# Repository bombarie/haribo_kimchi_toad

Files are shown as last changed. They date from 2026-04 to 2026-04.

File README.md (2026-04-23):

# Jaha Koo - Toad

Code and PCB design for the transmitter and receiver + driver board to control the Toad robot. The wireless control is achieved ising an ExpressLRS wireless link, controlled and read using arduino-compatible microcontrollers. The Toad uses Dynamixel smart servo motors. The host board in the Toad contains a Dynamixel motor driver board, an open-source board designed by [Josue Alejandro Gutierrez](https://github.com/JosueAGtz/dynamixelInterface) and fabbed by me.

Produced for [Campo](https://campo.nu).

## Current files
* Code
  * Toad control from desktop (Chataigne) - [toad_v07_increment_CCs](./chataigne/toad_v07_increment_CCs.noisette)
  * Midi-host transmitter code
    * transmitter #1 (Wemos S2 mini) - [CRServoF_lib_tx_v02_add_midi.cpp](/arduino/platformio/WEMOS_ESP32S2_MIDI_ELRSTX/src/CRServoF_lib_tx_v02_add_midi.cpp)
    * transmitter #2  (Wemos S3 mini) - [CRServoF_lib_tx_v02_add_midi.cpp](./arduino/platformio/wemos_s3_mini/src/CRServoF_lib_tx_v02_add_midi.cpp)
  * Toad receiver code (Xiao esp32-c3): [toad_dynamixel_examples_moveServo_v08_update_to_arduino_core_3.cpp](./arduino/platformio/esp32c3_helloworld/esp32c3_helloworld/src/toad_dynamixel_examples_moveServo_v08_update_to_arduino_core_3.cpp)
* PCB - [toad_mainboard_v03](./kicad/toad%20mainboard%20v01/toad_mainboard_v03/toad_mainboard_v03.kicad_pro)

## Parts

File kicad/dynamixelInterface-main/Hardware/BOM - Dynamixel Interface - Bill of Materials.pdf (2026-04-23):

# BOM - Dynamixel Interface

# | Reference | Part Number | Description | Manufacturer | Distribuitor | Quantity

1 | U1 | TXB0104PWR | Translation - Voltage Levels 4-Bit Bi-directional V-Level Translator | TI | MOUSER | 1
2 | U2 | SN74LVC2G241DCTR | Buffers & Line Drivers Tri-State Dual | TI | MOUSER | 1
3 | R1, R2, R3, R4 | ERJ-2RKF1001X | Thick Film Resistors - SMD 0402 1KOhm 1% AEC-Q200 | PANASONIC | MOUSER | 4
4 | R5 | ERJ-2RKF1002X | Thick Film Resistors - SMD 0402 10KOhms 1% AEC-Q200 | PANASONIC | MOUSER | 1
5 | C1 | 885012105012 | Multilayer Ceramic Capacitors MLCC - SMD/SMT WCAP-CSGP 1uF 0402 20% 10V MLCC | WE | MOUSER | 1
6 | C2, C5 | 885012205037 | Multilayer Ceramic Capacitors MLCC - SMD/SMT WCAP-CSGP 0.1uF 0402 10% 16V MLCC | WE | MOUSER | 2
7 | C3 | 885012206076 | Multilayer Ceramic Capacitors MLCC - SMD/SMT WCAP-CSGP 1uF 0603 10% 25V MLCC | WE | MOUSER | 1
8 | C4 | 885012106031 | Multilayer Ceramic Capacitors MLCC - SMD/SMT WCAP-CSGP 10uF 25Vol 20% | WE | MOUSER | 1
9 | D1, D2 | APHHS1005SECK | Standard LEDs - SMD ORANGE WTR CLEAR 160mcd 610nm | KINGBRIGHT | MOUSER | 2
10 | D3 | APHHS1005QBC/D | Standard LEDs - SMD Blue 470nm Water Clear | KINGBRIGHT | MOUSER | 1
11 | D4 | APHHS1005CGCK | Standard LEDs - SMD GREEN WTR CLEAR 40mcd 574nm | KINGBRIGHT | MOUSER | 1

Optional

12 | J1 | 22-05-7035 | Headers & Wire Housings 3 CKT 2.5MM R/A HDR | MOLEX | MOUSER | 1
13 | J1 | S3B-EH(LF)(SN) | CONN HEADER R/A 3POS 2.5MM | JST | DIGIKEY | 1

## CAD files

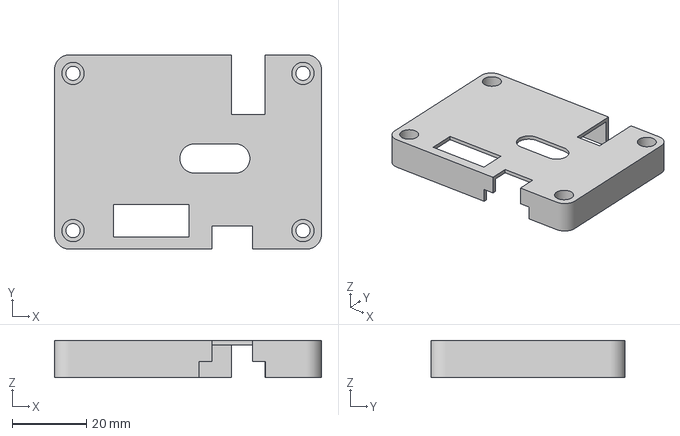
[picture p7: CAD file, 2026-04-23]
3mf/Jaha Koo - Toad - pcb housing v1 - bottom.3mf
72.0 x 52.4 x 10.0 mm

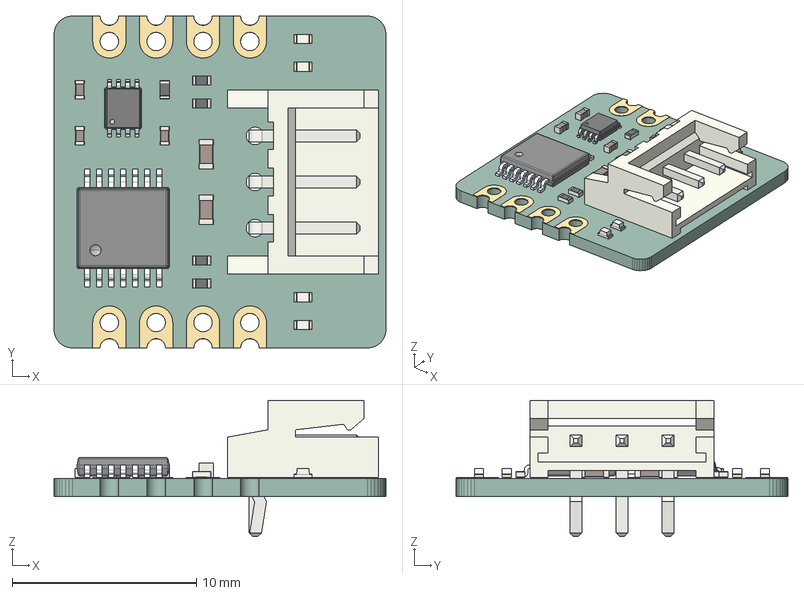
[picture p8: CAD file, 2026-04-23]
kicad/dynamixelInterface-main/Hardware/Dynamixel Interface.step
18.0 x 18.0 x 7.40 mm
PCB

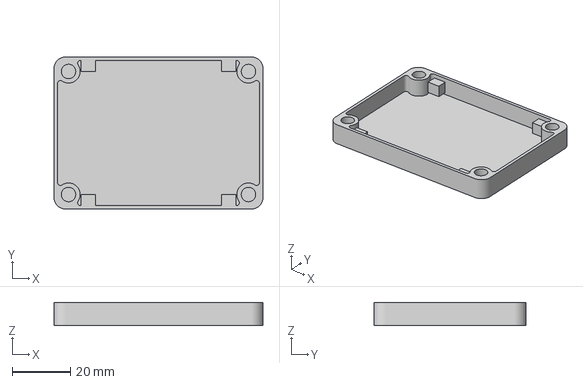
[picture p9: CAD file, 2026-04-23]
3mf/Jaha Koo - Toad - pcb housing v1 - top.3mf
72.0 x 52.4 x 8.00 mm

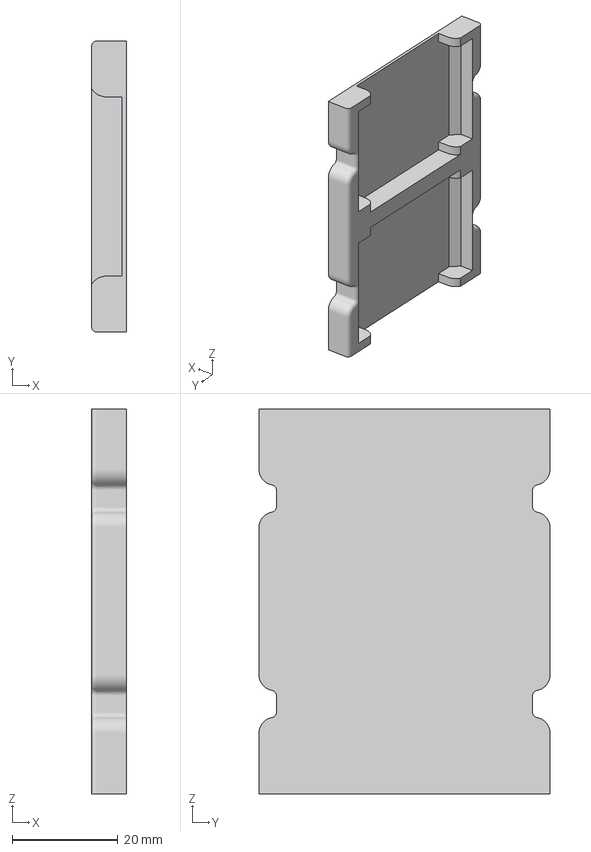
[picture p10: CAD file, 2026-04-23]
3mf/Jaha Koo - Toad - servo motor mount.3mf
6.61 x 55.1 x 72.8 mm

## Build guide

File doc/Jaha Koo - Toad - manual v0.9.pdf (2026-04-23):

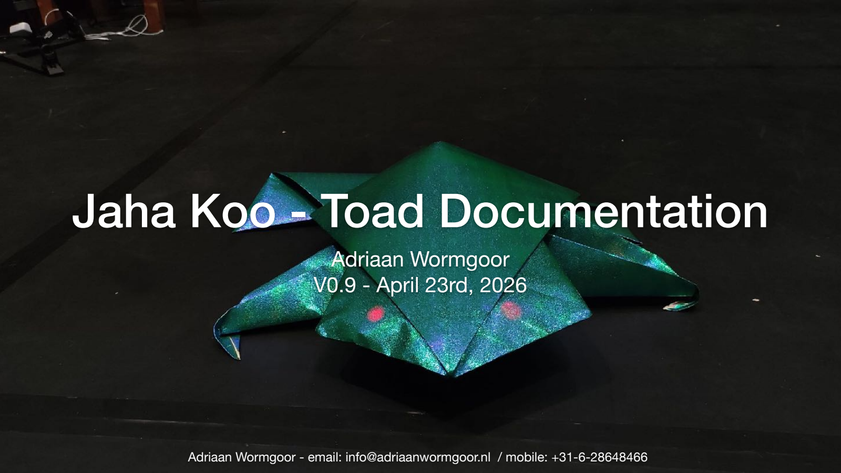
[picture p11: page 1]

Adriaan Wormgoor - email: info@adriaanwormgoor.nl / mobile: +31-6-28648466

# Jaha Koo - Toad Documentation

## Adriaan Wormgoor V0.9 - April 23rd, 2026

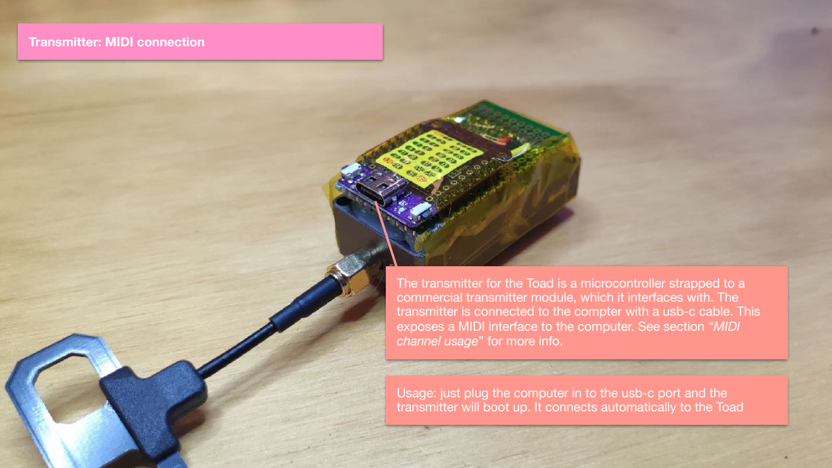
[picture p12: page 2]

Transmitter: MIDI connection

The transmitter for the Toad is a microcontroller strapped to a commercial transmitter module, which it interfaces with. The transmitter is connected to the compter with a usb-c cable. This exposes a MIDI interface to the computer. See section “MIDI channel usage” for more info.

Usage: just plug the computer in to the usb-c port and the transmitter will boot up. It connects automatically to the Toad

- When plugged in to the computer (using the usb-c port on the transmitter), the computer should detect a new MIDI device. The transmitter does not need to be switched on for this.
- All MIDI commands should be Control Change (CC) commands, over MIDI Channel 1.

CC 1, range [0-127]**

CC 2, range [0-127]**

Left motor - range 62->0 is backward speed, range 64->127 is forward speed. Value 63 = stopped

Right motor

CC 3, range [0-127]

CC 4, range [0-127]

Left eye

Right eye

**Range 62->0 = backward speed. Range 64->127 = forward speed. Value 63 = stopped

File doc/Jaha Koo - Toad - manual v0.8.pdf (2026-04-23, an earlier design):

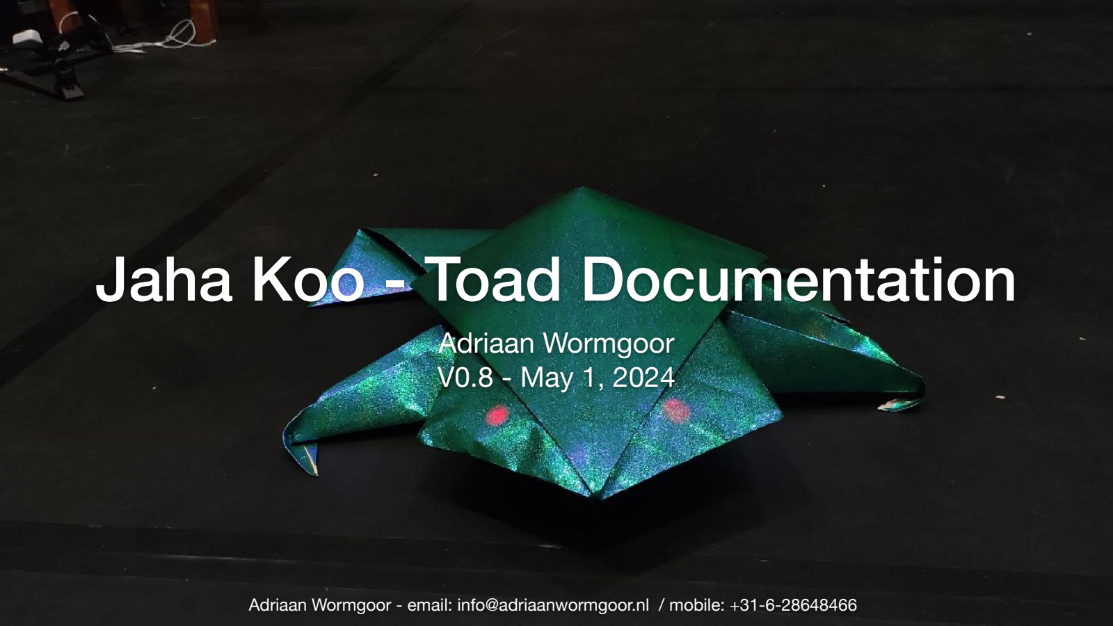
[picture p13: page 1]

Adriaan Wormgoor - email: info@adriaanwormgoor.nl / mobile: +31-6-28648466

# Jaha Koo - Toad Documentation

## Adriaan Wormgoor V0.8 - May 1, 2024


Transmitter: MIDI connection

The transmitter for the Toad is a microcontroller strapped to a commercial transmitter module, which it interfaces with. The transmitter is connected to the compter with a usb-c cable. This exposes a MIDI interface to the computer. See section “MIDI channel usage” for more info.

Usage: just plug the computer in to the usb-c port and the transmitter will boot up. It connects automatically to the Toad

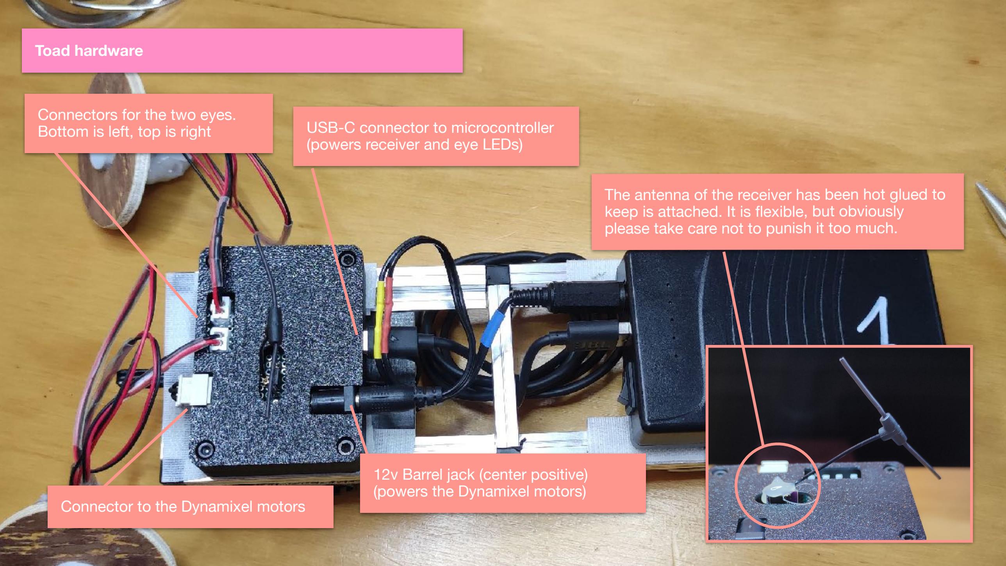
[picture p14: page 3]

Toad hardware

Connectors for the two eyes. Bottom is left, top is right

Connector to the Dynamixel motors

USB-C connector to microcontroller (powers receiver and eye LEDs)

12v Barrel jack (center positive) (powers the Dynamixel motors)

The antenna of the receiver has been hot glued to keep is attached. It is flexible, but obviously please take care not to punish it too much.

Toad hardware - receiver

When the microcontroller is switched on (usb-c port), the receiver will be powered. Its green LED will flash regularly to indicate it is looking for a connection, and become solid green when connected.

PLEASE always have the transmitter module (at the pc) powered first. This ensures a speedy connection. If the receiver hasn’t made a connection within 60 seconds, it will go into a maintenance mode (rapid flashing), after which connecting is not possible. You will have to power cycle the Toad before a connection is possible again (ie: turn the battery pack off and on again).

- When plugged in to the computer (using the usb-c port on the transmitter), the computer should detect a new MIDI device. The transmitter does not need to be switched on for this.
- All MIDI commands should be Control Change (CC) commands, over MIDI Channel 1.

MIDI channel usage

CC 0, range [0-127]**

CC 1, range [0-127]**

Left motor - range 62->0 is backward speed, range 64->127 is forward speed. Value 63 = stopped

Right motor

CC 2, range [0-127]

CC 3, range [0-127]

Left eye

Right eye

**Range 62->0 = backward speed. Range 64->127 = forward speed. Value 63 = stopped

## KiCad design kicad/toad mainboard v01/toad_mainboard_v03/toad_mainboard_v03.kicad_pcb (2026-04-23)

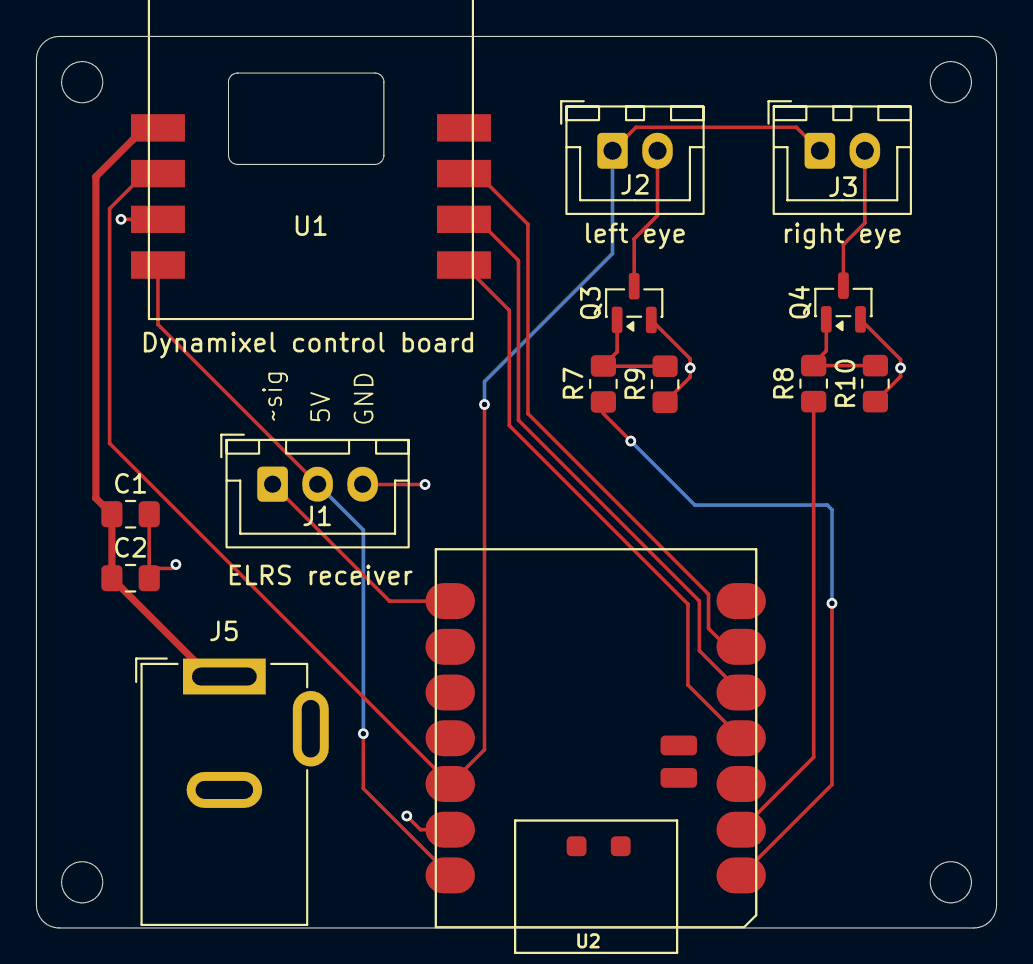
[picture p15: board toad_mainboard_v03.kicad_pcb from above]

Board: 2 copper layers, 53.3 x 49.5 mm, 14 parts (0 on the bottom side), 14 nets.

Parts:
C1: 1uF; C_0805_2012Metric_Pad1.18x1.45mm_HandSolder
C2: 0.1uF; C_0805_2012Metric_Pad1.18x1.45mm_HandSolder
J1: ELRS receiver; JST_XH_B3B-XH-A_1x03_P2.50mm_Vertical
J2: left eye; JST_XH_B2B-XH-A_1x02_P2.50mm_Vertical
J3: right eye; JST_XH_B2B-XH-A_1x02_P2.50mm_Vertical
J5: Barrel_Jack_Switch; BarrelJack_GCT_DCJ200-10-A_Horizontal
Q3, Q4: BC847; SOT-23
R7, R8: 330; R_0805_2012Metric_Pad1.20x1.40mm_HandSolder
R9, R10: 1k; R_0805_2012Metric_Pad1.20x1.40mm_HandSolder
U1: Dynamixel control board; Dynamixel_driver_board
U2: MOUDLE-SEEEDUINO-XIAO-ESP32C3; MOUDLE14P-SMD-2.54-21X17.8MM

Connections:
3.3V: J2.1, J3.1, U1.6 (VDD), U2.12 (3V3)
5V: J1.2, U1.8 (VCC), U2.14 (5V)
+12V: C1.1, C2.1, J5.1, U1.5 (VMOT)
DMXL_CTRL: U1.3 (CTRL), U2.6 (PA9_A5_D5_SCL)
DMXL_RX: U1.2 (TX), U2.5 (PA8_A4_D4_SDA)
DMXL_TX: U1.1 (RX), U2.4 (PA11_A3_D3)
ELRS_TX: J1.1, U2.8 (PB09_A7_D7_RX)
GND: C1.2, C2.2, J1.3, J5.2, Q3.2 (E), Q4.2 (E), R9.1, R10.1, U1.7 (GND), U2.13 (GND)
LEFT_EYE: R7.1, U2.1 (PA02_A0_D0)
unnamed: J2.2, Q3.3 (C)
unnamed: J3.2, Q4.3 (C)
unnamed: Q3.1 (B), R7.2, R9.2
unnamed: Q4.1 (B), R8.2, R10.2
RIGHT_EYE: R8.1, U2.2 (PA4_A1_D1)

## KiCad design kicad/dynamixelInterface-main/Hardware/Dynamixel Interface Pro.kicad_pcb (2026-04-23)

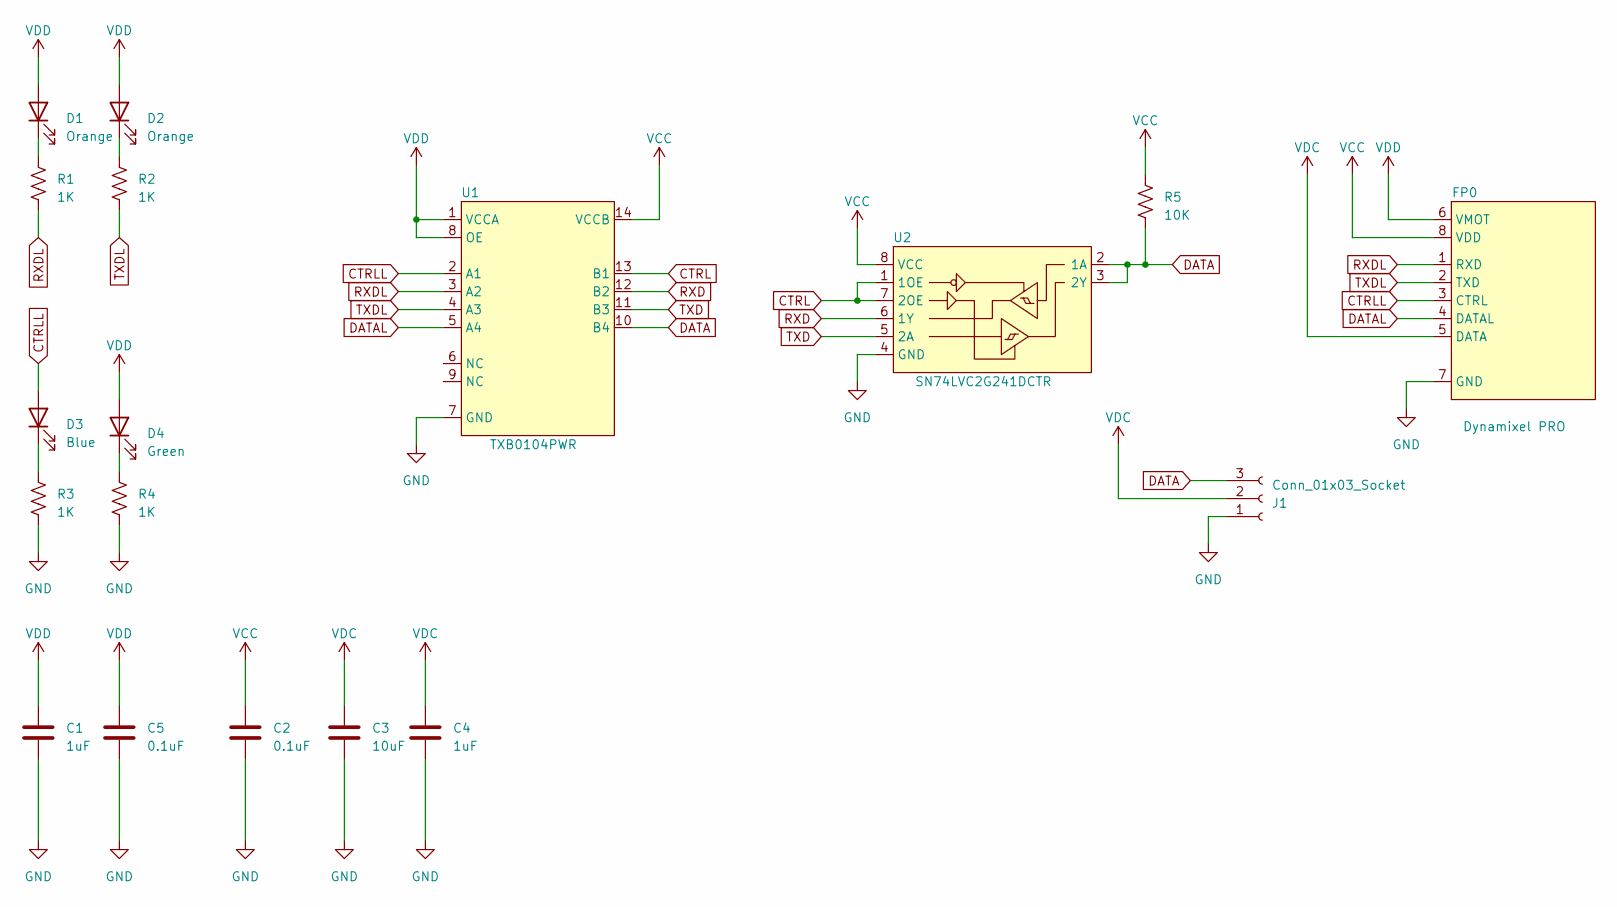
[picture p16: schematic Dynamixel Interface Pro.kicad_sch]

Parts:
C1: 1uF; C_0402_1005Metric
C2, C5: 0.1uF; C_0402_1005Metric
C3: 10uF; C_0603_1608Metric
C4: 1uF; C_0603_1608Metric
D1, D2: Orange; 0402LED
D3: Blue; 0402LED
D4: Green; 0402LED
FP0: Dynamixel PRO; Dynamixel_Driver
J1: Conn_01x03_Socket; JST_EH_S3B-EH_1x03_P2.50mm_Horizontal
R1, R2, R3, R4: 1K; R_0402_1005Metric
R5: 10K; R_0402_1005Metric
U1: TXB0104PWR; TSSOP14_5x4.4_0.65
U2: SN74LVC2G241DCTR; VSSOP-8_2.3x2mm_P0.5mm

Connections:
CTRL: U1.13 (B1), U2.1 (1OE), U2.7 (2OE)
CTRLL: D3.2 (A), FP0.3 (CTRL), U1.2 (A1)
DATA: J1.3, R5.2, U1.10 (B4), U2.2 (1A), U2.3 (2Y)
DATAL: FP0.4 (DATAL), U1.5 (A4)
GND: C1.2, C2.2, C3.2, C4.2, C5.2, FP0.7 (GND), J1.1, R3.2, R4.2, U1.7 (GND), U2.4 (GND)
unnamed: D1.1 (K), R1.1
unnamed: D2.1 (K), R2.1
unnamed: D3.1 (K), R3.1
unnamed: D4.1 (K), R4.1
RXD: U1.12 (B2), U2.6 (1Y)
RXDL: FP0.1 (RXD), R1.2, U1.3 (A2)
TXD: U1.11 (B3), U2.5 (2A)
TXDL: FP0.2 (TXD), R2.2, U1.4 (A3)
VCC: C2.1, FP0.8 (VDD), R5.1, U1.14 (VCCB), U2.8 (VCC)
VDC: C3.1, C4.1, FP0.5 (DATA), J1.2
VDD: C1.1, C5.1, D1.2 (A), D2.2 (A), D4.2 (A), FP0.6 (VMOT), U1.1 (VCCA), U1.8 (OE)

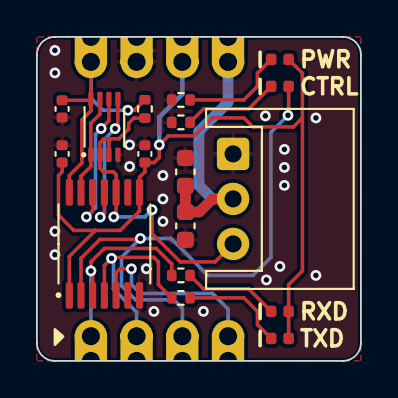
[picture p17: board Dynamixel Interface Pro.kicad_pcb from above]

Board: 2 copper layers, 18.0 x 18.0 mm, 19 parts (1 on the bottom side), 16 nets.

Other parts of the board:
G_logoSmall: LOGO; G_SELOGO_SMALL

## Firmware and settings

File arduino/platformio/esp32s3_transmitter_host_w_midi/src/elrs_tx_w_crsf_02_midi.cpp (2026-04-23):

#include <Arduino.h>
#include <Adafruit_TinyUSB.h>
#include <MIDI.h>

/*
// Simple Arduino trasmisster
// Arduino Nano
// ELRS 2.4G TX moduel
// Custom PCB from JLCPCB
// const float codeVersion = 0.92; // Software revision
// https://github.com/kkbin505/Arduino-Transmitter-for-ELRS

 * This file is part of Simple TX
 *
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
 * You should have received a copy of the GNU General Public License
 * along with Cleanflight.  If not, see <http://www.gnu.org/licenses/>.
 */

#include "EEPROM.h"
#include "config.h"
#include "crsf.h"
#include "led.h"
#include "tone.h"

// #define DEBUG // if not commented out, Serial.print() is active! For debugging only!!
// #define GIMBAL_CALIBRATION //

// USB MIDI object
Adafruit_USBD_MIDI usb_midi;

// Create a new instance of the Arduino MIDI Library,
// and attach usb_midi as the transport.
MIDI_CREATE_INSTANCE(Adafruit_USBD_MIDI, usb_midi, MIDI);

void printBytes(const byte *data, unsigned int size);

void handleNoteOn(byte channel, byte pitch, byte velocity);
void handleNoteOff(byte channel, byte pitch, byte velocity);
void handleControlChange(byte channel, byte data1, byte data2);

enum DEADBAND_INPUT_RANGE
{
    _256 = 127,
    _1024 = 1023
};

byte ledPWMVal = 0;
byte audioVal = 0;
byte bodyExpressionVal = 0;
byte aux1_val = 0;
byte aux2_val = 0;
byte aux3_val = 0;

uint16_t neopixelHVal = 0;
byte neopixelSVal = 0;
byte neopixelVVal = 0;

byte neopixel_rVal = 0;
byte neopixel_gVal = 0;
byte neopixel_bVal = 0;

byte bitmash_nood1a = 0;
byte bitmash_nood1b = 0;
byte bitmash_nood2a = 0;
byte bitmash_nood2b = 0;

#define LED_PIN 3
#define NOODS_OUT_PIN 39
#define PWM_OUT_1 37
#define AUX1_PIN 35
#define AUX2_PIN 33
#define AUX3_PIN 18

byte channelToPrint = 255;

unsigned long prevSerialPrintMills;
unsigned long serialPrintInterval = 200;

unsigned long prevBitmashChangeChannelMills;
unsigned long bitmashChangeChannelInterval = 10;
byte bitmashSendChannel = 0;

uint16_t bitmashed_out = 0;
uint16_t bitmashed_outs[] = {0, 0, 0, 0};

// FYI -> I manually explored when the values at the receiver start moving.
// 'deadbandLowerThreshold' is the percentage at the bottom of the range where the values start to move.
// 'deadbandUpperThreshold' is the percentage at the top of the range where the values start to move.
float deadbandLowerThreshold = 0.125; // everything lower than this percentage is capped off on the receiving end
float deadbandUpperThreshold = 0.915; // everything higher than this percentage is capped off on the receiving end

// methods
void writeValuesToOutputs();
void overrideNoodOutputValues();
void BlinkLed(byte num);
void updateSelectedNoodSendIndex();
void calcNoodOutputValues();
void updateSerialPrintValues();
void serialPrintDebugValues();

void BlinkLed(byte num) // Basic blink function
{
    for (byte i = 0; i < num; i++)
    {
        digitalWrite(LED_BUILTIN, HIGH);
        delay(50);
        digitalWrite(LED_BUILTIN, LOW);
        delay(50);
    }
}

int Aileron_value = 0; // values read from the pot
int Elevator_value = 0;
int Throttle_value = 0;
int Rudder_value = 0;
int previous_throttle = 191;

int loopCount = 0; // for ELRS seeting

int AUX1_Arm = 0; // switch values read from the digital pin
int AUX2_value = 0;
int AUX3_value = 0;
int AUX4_value = 0;

float batteryVoltage;

int currentPktRate = 0;
int currentPower = 0;
int currentSetting = 0;
int stickMoved = 0;
int stickInt = 0;
uint32_t stickMovedMillis = 0;

uint32_t currentMillis = 0;

uint8_t crsfPacket[CRSF_PACKET_SIZE];
uint8_t crsfCmdPacket[CRSF_CMD_PACKET_SIZE];
int16_t rcChannels[CRSF_MAX_CHANNEL];
uint32_t crsfTime = 0;

CRSF crsfClass;

bool calStatus = false;

// -----------------------------------------------------------------------------------------------------
// Calibration

#define CALIB_MARK 0x55
#define CALIB_MARK_ADDR 0x00
#define CALIB_VAL_ADDR CALIB_MARK_ADDR + 1

#define CALIB_CNT 5         // times of switch on/off
#define CALIB_CENT_TMO 5000 // ms
#define CALIB_TMO 20000     // ms
int cal_reset = 0;

struct CalibValues
{
    int aileronMin;
    int aileronMax;
    int aileronCenter;
    int elevatorMin;
    int elevatorMax;
    int elevatorCenter;
    int thrMin;
    int thrMax;
    int rudderMin;
    int rudderMax;
    int rudderCenter;
};

CalibValues calValues;

void selectSetting();
bool checkStickMove();
void calibrationRun(int aux1, int aux2);
bool calibrationRequested();
bool calibrationProcess();
void calibrationCount(int aux1, int aux2);
void calibrationChirp(uint8_t times);
bool calibrationPresent();
void calibrationSave();
void calibrationLoad();
void calibrationReset();

bool calibrationPresent()
{
    return EEPROM.read(CALIB_MARK_ADDR) == CALIB_MARK;
}

void calibrationSave()
{
    EEPROM.write(CALIB_MARK_ADDR, CALIB_MARK);
    EEPROM.put(CALIB_VAL_ADDR, calValues);
    EEPROM.commit();
}

void calibrationLoad()
{
    EEPROM.get(CALIB_VAL_ADDR, calValues);
}

void calibrationReset()
{
    EEPROM.put(CALIB_MARK_ADDR, (uint8_t)0xFF);
    calValues = {
        .aileronMin = ANALOG_CUTOFF,
        .aileronMax = 8191 - ANALOG_CUTOFF,
        .aileronCenter = 988,
        .elevatorMin = ANALOG_CUTOFF,
        .elevatorMax = 8191 - ANALOG_CUTOFF,
        .elevatorCenter = 988,
        .thrMin = ANALOG_CUTOFF,
        .thrMax = 8191 - ANALOG_CUTOFF,
        .rudderMin = ANALOG_CUTOFF,
        .rudderMax = 8191 - ANALOG_CUTOFF,
        .rudderCenter = 988,
    };
    EEPROM.put(CALIB_VAL_ADDR, calValues);
    EEPROM.commit();
}

uint8_t aux2cnt = 0;

unsigned long calibrationTimerStart;

// Flash LED and beep for (times)
void calibrationChirp(uint8_t times)
{

    digitalWrite(DIGITAL_PIN_LED, HIGH);
    delay(1000);
    digitalWrite(DIGITAL_PIN_LED, LOW);
    delay(1000);

    for (uint8_t i = 0; i < times; i++)
    {
        digitalWrite(DIGITAL_PIN_BUZZER, HIGH);
        digitalWrite(DIGITAL_PIN_LED, HIGH);
        delay(100);
        digitalWrite(DIGITAL_PIN_BUZZER, LOW);
        digitalWrite(DIGITAL_PIN_LED, LOW);
        delay(100);
    }
    digitalWrite(DIGITAL_PIN_LED, LOW);
}

void calibrationCount(int aux1, int aux2)
{
    static uint8_t preAux2 = 0;

    // Don't do anything if ARMED
    if (aux1 != 0)
    {
        aux2cnt = 0;
        preAux2 = 0;
        return;
    }

    else
    {
        // Start timer window // Arm = DISARMED
        if (aux2cnt == 0)
        {
            calibrationTimerStart = millis();
        }

        // Timeout
        if (calibrationTimerStart + CALIB_TMO > millis())
        {
            aux2cnt = 0;
            preAux2 = 0;
            return;
        }

        // Analyze AUX2 switch, count only one side of the switch
        if (aux2 == 1 && preAux2 == 0)
        {
            aux2cnt++;
            preAux2 = 1;
        }
        else if (aux2 == 0 && preAux2 == 1)
        {
            preAux2 = 0;
        }
    }
}

bool calibrationRequested()
{
    // return aux2cnt > CALIB_CNT;
    return calStatus;
}

bool calibrationProcess()
{
    aux2cnt = 0;

    // calibrationChirp(2);    // start calibration

    // Reset variables to "centers"

    while (cal_reset < 1)
    {
        const int centerValue = (8191 - ANALOG_CUTOFF - ANALOG_CUTOFF) / 2;
        calValues.aileronMin = centerValue;
        calValues.aileronMax = centerValue;
        calValues.aileronCenter = centerValue;
        calValues.elevatorMin = centerValue;
        calValues.elevatorMax = centerValue;
        calValues.elevatorCenter = centerValue;
        calValues.thrMin = centerValue;
        calValues.thrMax = centerValue;
        calValues.rudderMin = centerValue;
        calValues.rudderMax = centerValue;
        calValues.rudderCenter = centerValue;
        cal_reset++;
    }

    currentMillis = millis();

    if (currentMillis < CALIB_CENT_TMO)
    {
        // A Center
        int val = analogRead(analogInPinAileron);
        calValues.aileronCenter = val;

        // E Center
        val = analogRead(analogInPinElevator);
        calValues.elevatorCenter = val;

        // R Center
        val = analogRead(analogInPinRudder);
        calValues.rudderCenter = val;

        Serial.print("Aileron_Min:");
        Serial.print("Center Stick: AilerCenter:");
        Serial.print(calValues.aileronCenter);
        Serial.print(" ElevatorCenter:");
        Serial.print(calValues.elevatorCenter);
        Serial.print(" RudderCenter:");
        Serial.print(calValues.rudderCenter);
        Serial.println();
    }
    // 15 seconds for moving sticks
    else if (currentMillis > CALIB_CENT_TMO && currentMillis < CALIB_TMO)
    {
        // while ((calibrationTimerStart + CALIB_TMO ) < millis()) {
        //  A Min-Max
        int val = analogRead(analogInPinAileron);
        if (val < calValues.aileronMin)
        {
            calValues.aileronMin = val;
        }
        if (val > calValues.aileronMax)
        {
            calValues.aileronMax = val;
        }
        // E Min-Max
        val = analogRead(analogInPinElevator);
        if (val < calValues.elevatorMin)
        {
            calValues.elevatorMin = val;
        }
        if (val > calValues.elevatorMax)
        {
            calValues.elevatorMax = val;
        }

        // T Min-Max
        val = analogRead(analogInPinThrottle);
        if (val < calValues.thrMin)
        {
            calValues.thrMin = val;
        }
        if (val > calValues.thrMax)
        {
            calValues.thrMax = val;
        }

        // R Min-Max
        val = analogRead(analogInPinRudder);
        if (val < calValues.rudderMin)
        {
            calValues.rudderMin = val;
        }
        if (val > calValues.rudderMax)
        {
            calValues.rudderMax = val;
        }

        // Double beep and blink every 500ms
        if (millis() % 500 == 0)
        {
            // calibrationChirp(2);
        }
        Serial.print("Mover stick full range: Aileron_Min:");
        Serial.print(calValues.aileronMin);
        Serial.print(" Max:");
        Serial.print(calValues.aileronMax);
        Serial.print(" ElevatorMin:");
        Serial.print(calValues.elevatorMin);
        Serial.print(" Max:");
        Serial.print(calValues.elevatorMax);
        Serial.print(" RudderMin:");
        Serial.print(calValues.rudderMin);
        Serial.print(" Max:");
        Serial.print(calValues.rudderMax);
        Serial.print(" ThrottleMin:");
        Serial.print(calValues.thrMin);
        Serial.print(" Max:");
        Serial.print(calValues.thrMax);
        Serial.println();
    }
    else
    {
        Serial.println("Calibration Done");
        calibrationSave();
        calStatus = false;
    }
    return true;
}

void calibrationRun(int aux1, int aux2)
{
    if (calibrationRequested())
    {
        // calibrationReset();
        if (calibrationProcess())
        {
            // calibrationSave();
            // calibrationChirp(3);    // ok
            // Serial.println("Calibration OK");
        }
        else
        {
            // calibrationReset();
            // calibrationChirp(10);   // error
            Serial.println("Calibration error!");
        }
    }
    else
    {
        calibrationCount(aux1, aux2);
    }
}

// -----------------------------------------------------------------------------------------------------

void selectSetting()
{
    // startup stick commands (protocol selection / renew transmitter ID)

    if (rcChannels[AILERON] < RC_MIN_COMMAND && rcChannels[ELEVATOR] < RC_MIN_COMMAND)
    { // Elevator down + aileron left
        currentPktRate = SETTING_1_PktRate;
        currentPower = SETTING_1_Power;
        currentSetting = 1;
    }
    else if (rcChannels[AILERON] > RC_MAX_COMMAND && rcChannels[ELEVATOR] > RC_MAX_COMMAND)
    { // Elevator up + aileron right
        currentPktRate = SETTING_2_PktRate;
        currentPower = SETTING_2_Power;
        currentSetting = 2;
    }
    else if (rcChannels[AILERON] < RC_MIN_COMMAND && rcChannels[ELEVATOR] > RC_MAX_COMMAND)
    { // Elevator up + aileron right
        currentPktRate = SETTING_3_PktRate;
        currentPower = SETTING_3_Power;
        currentSetting = 3;
    }
    else
    {
        currentSetting = 0;
    }
}

bool checkStickMove()
{
    // check if stick moved, warring after 10 minutes
    if (abs(previous_throttle - rcChannels[THROTTLE]) < 30)
    {
        stickMoved = 0;
        // Serial.println(abs(previous_throttle - rcChannels[THROTTLE]));
    }
    else
    {
        previous_throttle = rcChannels[THROTTLE];
        stickMovedMillis = millis();
        stickMoved = 1;
    }

    if (millis() - stickMovedMillis > STICK_ALARM_TIME)
    {
        // Serial.println((millis() - stickMovedMillis));
        return true;
    }
    else
    {
        return false;
    }
}

void setup()
{
    usb_midi.setStringDescriptor("TinyUSB MIDI");

    // Initialize MIDI, and listen to all MIDI channels
    // This will also call usb_midi's begin()
    MIDI.begin(MIDI_CHANNEL_OMNI);

    MIDI.setHandleNoteOn(handleNoteOn);
    MIDI.setHandleNoteOff(handleNoteOff);
    MIDI.setHandleControlChange(handleControlChange);

    // Serial.begin(115200);

    // wait until device mounted
    while (!TinyUSBDevice.mounted())
        delay(1);

    // inialize rc data
    for (uint8_t i = 0; i < CRSF_MAX_CHANNEL; i++)
    {
        rcChannels[i] = CRSF_DIGITAL_CHANNEL_MIN;
    }

    // analogReference(EXTERNAL);

    pinMode(DIGITAL_PIN_SWITCH_ARM, INPUT_PULLUP);
    pinMode(DIGITAL_PIN_SWITCH_AUX2, INPUT_PULLUP);
    pinMode(DIGITAL_PIN_SWITCH_AUX3, INPUT_PULLUP);
    // pinMode(DIGITAL_PIN_SWITCH_AUX4, INPUT_PULLUP);
    pinMode(DIGITAL_PIN_LED, OUTPUT);    // LED
    pinMode(DIGITAL_PIN_BUZZER, OUTPUT); // LED
    // digitalWrite(DIGITAL_PIN_BUZZER, LOW);
    // inialize voltage:
    batteryVoltage = 0.0;

    delay(1000); // Give enough time for uploda firmware 1 second

#ifdef DEBUG
    Serial.begin(115200);
#else
    // Serial2.begin(115200, SERIAL_8N1, 37, 39);
    crsfClass.begin();
#endif

#ifdef GIMBAL_CALIBRATION
    Serial.begin(115200);
    // calibrationReset();
    calStatus = true;
    Serial.println("Start Calibration");
#endif

    digitalWrite(DIGITAL_PIN_LED, HIGH); // LED ON
    // digitalWrite(DIGITAL_PIN_BUZZER, HIGH); // BUZZER OFF

    calibrationReset();
    calibrationLoad();

    // Set channels [0-4] (ie override left/right motor and left/right eye).
    // Channel order: AETR
    rcChannels[AILERON] = (CRSF_DIGITAL_CHANNEL_MIN + CRSF_DIGITAL_CHANNEL_MAX) / 2;
    rcChannels[ELEVATOR] = (CRSF_DIGITAL_CHANNEL_MIN + CRSF_DIGITAL_CHANNEL_MAX) / 2;
    rcChannels[THROTTLE] = CRSF_DIGITAL_CHANNEL_MIN;
    rcChannels[RUDDER] = CRSF_DIGITAL_CHANNEL_MIN;
}

void loop()
{
#ifdef GIMBAL_CALIBRATION
    if (calStatus)
    {
        calibrationRun(AUX1_Arm, AUX2_value);
    }
#endif

    uint32_t currentMicros = micros();

    // Read Voltage
    batteryVoltage = analogRead(VOLTAGE_READ_PIN) / 103.0f; // 98.5

    if (batteryVoltage < WARNING_VOLTAGE && batteryVoltage >= BEEPING_VOLTAGE)
    {
        blinkLED(DIGITAL_PIN_LED, 1000);
    }
    else if (batteryVoltage < BEEPING_VOLTAGE)
    {
        blinkLED(DIGITAL_PIN_LED, 300);
        playingTones(2);
    }

    if (checkStickMove() == true)
    {
        blinkLED(DIGITAL_PIN_LED, 100);
        playingTones(5);
    }

    /*
     * Handle analogy input
     */
    // constrain to avoid overflow
    int analogVal = analogRead(analogInPinAileron);
    if (analogVal <= calValues.aileronCenter)
    {
        Aileron_value = map(analogVal, calValues.aileronMin, calValues.aileronCenter, ADC_MIN, ADC_MID);
    }
    else
    {
        Aileron_value = map(analogVal, calValues.aileronCenter, calValues.aileronMax, ADC_MID + 1, ADC_MAX);
    }

    analogVal = analogRead(analogInPinElevator);
    if (analogVal <= calValues.elevatorCenter)
    {
        Elevator_value = map(analogVal, calValues.elevatorMin, calValues.elevatorCenter, ADC_MIN, ADC_MID);
    }
    else
    {
        Elevator_value = map(analogVal, calValues.elevatorCenter, calValues.elevatorMax, ADC_MID + 1, ADC_MAX);
    }

    analogVal = analogRead(analogInPinThrottle);
    Throttle_value = map(analogVal, calValues.thrMax, calValues.thrMin, ADC_MIN, ADC_MAX);

    analogVal = analogRead(analogInPinRudder);
    if (analogVal <= calValues.rudderCenter)
    {
        Rudder_value = map(analogVal, calValues.rudderMin, calValues.rudderCenter, ADC_MIN, ADC_MID);
    }
    else
    {
        Rudder_value = map(analogVal, calValues.rudderCenter, calValues.rudderMax, ADC_MID + 1, ADC_MAX);
    }

    // Constrain value to avoid overflow
    Aileron_value = constrain(Aileron_value, ADC_MIN, ADC_MAX);
    Elevator_value = constrain(Elevator_value, ADC_MIN, ADC_MAX);
    Throttle_value = constrain(Throttle_value, ADC_MIN, ADC_MAX);
    Rudder_value = constrain(Rudder_value, ADC_MIN, ADC_MAX);

    // Handdle reverse
    if (Is_Aileron_Reverse == 1)
    {
        Aileron_value = 8191 - Aileron_value;
    }
    if (Is_Elevator_Reverse == 1)
    {
        Elevator_value = 8191 - Elevator_value;
    }
    if (Is_Throttle_Reverse == 1)
    {
        Throttle_value = 8191 - Throttle_value;
    }
    if (Is_Rudder_Reverse == 1)
    {
        Rudder_value = 8191 - Rudder_value;
    }
    // rcChannels[AILERON] = map(Aileron_value, 1023 - ANALOG_CUTOFF, ANALOG_CUTOFF, CRSF_DIGITAL_CHANNEL_MIN, CRSF_DIGITAL_CHANNEL_MAX);   // reverse
    // rcChannels[ELEVATOR] = map(Elevator_value, 1023 - ANALOG_CUTOFF, ANALOG_CUTOFF, CRSF_DIGITAL_CHANNEL_MIN, CRSF_DIGITAL_CHANNEL_MAX); // reverse
    // rcChannels[THROTTLE] = map(Throttle_value, 1023 - ANALOG_CUTOFF, ANALOG_CUTOFF, CRSF_DIGITAL_CHANNEL_MIN, CRSF_DIGITAL_CHANNEL_MAX); // reverse
    // rcChannels[RUDDER] = map(Rudder_value, ANALOG_CUTOFF, 1023 - ANALOG_CUTOFF, CRSF_DIGITAL_CHANNEL_MIN, CRSF_DIGITAL_CHANNEL_MAX);

    /*
    rcChannels[AILERON] = map(Aileron_value, ADC_MIN, ADC_MAX, CRSF_DIGITAL_CHANNEL_MIN, CRSF_DIGITAL_CHANNEL_MAX);
    rcChannels[ELEVATOR] = map(Elevator_value, ADC_MIN, ADC_MAX, CRSF_DIGITAL_CHANNEL_MIN, CRSF_DIGITAL_CHANNEL_MAX);
    rcChannels[THROTTLE] = map(Throttle_value, ADC_MIN, ADC_MAX, CRSF_DIGITAL_CHANNEL_MIN, CRSF_DIGITAL_CHANNEL_MAX);
    rcChannels[RUDDER] = map(Rudder_value, ADC_MIN, ADC_MAX, CRSF_DIGITAL_CHANNEL_MIN, CRSF_DIGITAL_CHANNEL_MAX);
    */

    /*
     * Handel digital input
     */
    AUX1_Arm = digitalRead(DIGITAL_PIN_SWITCH_ARM);
    AUX2_value = digitalRead(DIGITAL_PIN_SWITCH_AUX2);
    AUX3_value = digitalRead(DIGITAL_PIN_SWITCH_AUX3);
    // AUX4_value = digitalRead(DIGITAL_PIN_SWITCH_AUX4);// reuse for LED

    // Aux Channels
    // rcChannels[AUX1] = (AUX1_Arm == 1) ? CRSF_DIGITAL_CHANNEL_MIN : CRSF_DIGITAL_CHANNEL_MAX;
    // rcChannels[AUX2] = (AUX2_value == 1) ? CRSF_DIGITAL_CHANNEL_MIN : CRSF_DIGITAL_CHANNEL_MAX;
    // rcChannels[AUX3] = (AUX3_value == 0) ? CRSF_DIGITAL_CHANNEL_MIN : CRSF_DIGITAL_CHANNEL_MAX;
    // rcChannels[AUX4] = (AUX4_value == 0) ? CRSF_DIGITAL_CHANNEL_MIN : CRSF_DIGITAL_CHANNEL_MAX;

    if (stickInt = 0)
    {
        previous_throttle = rcChannels[THROTTLE];
        stickInt = 1;
    }
    selectSetting();

    if (currentMicros > crsfTime)
    {
#ifdef DEBUG
        // Serial.println("DEBUG");
        Serial.print(" AILERON:");
        Serial.print(rcChannels[AILERON]);
        Serial.print(", ELEVATOR:");
        Serial.print(rcChannels[ELEVATOR]);

        Serial.print(", Throttle_value:");
        Serial.print(Throttle_value);
        Serial.print(", calValues.thrMin:");
        Serial.print(calValues.thrMin);
        Serial.print(", calValues.thrMax:");
        Serial.print(calValues.thrMax);

        Serial.print(", THROTTLE:");
        Serial.print(rcChannels[THROTTLE]);
        Serial.print(", RUDDER:");
        Serial.print(rcChannels[RUDDER]);
        Serial.print(", stickstatus:");
        Serial.print(stickMoved);
        Serial.print(", previous_throttle:");
        Serial.print(previous_throttle);

        Serial.print(", currentSetting:");
        Serial.print(currentSetting);
        Serial.print(", currentPktRate:");
        Serial.print(currentPktRate);
        Serial.print(", currentPower:");
        Serial.print(currentPower);
        Serial.println();

#else
        if (loopCount <= 500)
        { // repeat 500 packets to build connection to TX module
            // Build commond packet
            crsfClass.crsfPrepareDataPacket(crsfPacket, rcChannels);
            crsfClass.CrsfWritePacket(crsfPacket, CRSF_PACKET_SIZE);
            loopCount++;
        }

        if (loopCount > 500 && loopCount <= 505)
        { // repeat 5 packets to avoid bad packet, change rate setting
            // Build commond packet
            if (currentSetting > 0)
            {
                crsfClass.crsfPrepareCmdPacket(crsfCmdPacket, ELRS_PKT_RATE_COMMAND, currentPktRate);
                // buildElrsPacket(crsfCmdPacket,ELRS_WIFI_COMMAND,0x01);
                crsfClass.CrsfWritePacket(crsfCmdPacket, CRSF_CMD_PACKET_SIZE);
            }
            loopCount++;
        }
        else if (loopCount > 505 && loopCount < 510)
        { // repeat 5 packets to avoid bad packet, change TX power level
            if (currentSetting > 0)
            {
                crsfClass.crsfPrepareCmdPacket(crsfCmdPacket, ELRS_POWER_COMMAND, currentPower);
                // buildElrsPacket(crsfCmdPacket,ELRS_WIFI_COMMAND,0x01);
                crsfClass.CrsfWritePacket(crsfCmdPacket, CRSF_CMD_PACKET_SIZE);
            }
            loopCount++;
        }
        else
        {
            crsfClass.crsfPrepareDataPacket(crsfPacket, rcChannels);
            crsfClass.CrsfWritePacket(crsfPacket, CRSF_PACKET_SIZE);
        }
#endif
        crsfTime = currentMicros + CRSF_TIME_BETWEEN_FRAMES_US;
    }

    // read any new MIDI messages
    // DO NOT USE 'DELAY()' -> the usbMIDI.read() needs to be called rapidly from loop()
    MIDI.read();
}
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

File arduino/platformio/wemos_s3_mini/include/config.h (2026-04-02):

/*
 * This file is part of Simple TX
 *
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
 * You should have received a copy of the GNU General Public License
 * along with Cleanflight.  If not, see <http://www.gnu.org/licenses/>.
 */

//#define USE_M7

/*
 =======================================================================================================
 Simple TX CONFIG OPTIONS (comment out unneeded options)
 =======================================================================================================
 */
// Define analogy input limite

#include <Arduino.h>

// #define ADC_MIN 0
// #define ADC_MID 511
// #define ADC_MAX 1023
#define ADC_MIN 0
#define ADC_MID 4095
#define ADC_MAX 8191


#define ANALOG_CUTOFF 150 // cut off lower and upper end to avoid un-symmetric joystick range in trade off resolution

// Define RC input Offset
#ifdef USE_M7
// M7
int Aileron_OFFSET    = -46;
int Elevator_OFFSET   = 57;
int Throttle_OFFSET   = 0;
int Rudder_OFFSET     = -18;
#else
// stat war
int Aileron_OFFSET    = 0;
int Elevator_OFFSET   = 0;
int Throttle_OFFSET   = 0;
int Rudder_OFFSET     = 0;
#endif

// Define Reverse 1=reverse
int Is_Aileron_Reverse  =1;
int Is_Elevator_Reverse =0;
int Is_Throttle_Reverse =1;
int Is_Rudder_Reverse   =0;

// IO setup
// pins that used for the Joystick
const int analogInPinAileron = 8;
const int analogInPinElevator = 7;
const int analogInPinThrottle = 3;
const int analogInPinRudder = 9;
const int VOLTAGE_READ_PIN = 11;

// pins that used for the switch
const int DIGITAL_PIN_SWITCH_ARM = 1;  // Arm switch
const int DIGITAL_PIN_SWITCH_AUX2 = 2; //
const int DIGITAL_PIN_SWITCH_AUX3 = 4;  //
// const int DIGITAL_PIN_SWITCH_AUX4 = 5;  //

// pins that used for output
const int DIGITAL_PIN_LED = LED_BUILTIN;    // in pcb v0.9 led is reused from AUX4 (remember to add 300om resistor in led)
//const int DIGITAL_PIN_BUZZER = 7; // do not use in pcb v0.9

// pins that used for buzzer
const int DIGITAL_PIN_BUZZER = 10;
//----- Voltage monitoring -------------------------
// Define battery warning voltage
const float WARNING_VOLTAGE = 7.4; // 2S Lipo 3.7v per cell
const float BEEPING_VOLTAGE = 7.0; // 2S Lipo 3.5v per cell

// Define Commond for start Up Setting
#define RC_MIN_COMMAND 600
#define RC_MAX_COMMAND 1400

// Define stick unmove alarm time
#define STICK_ALARM_TIME 30000

// from https://github.com/DeviationTX/deviation/pull/1009/ ELRS menu implement in deviation TX
/*static uint8_t  currentPktRate =1; //  "250Hz", "150Hz", "50Hz"
  //                                       1        3       5
static uint8_t  currentPower =1 ;//  "10mW", "25mW", "50mW", "100mW", "250mW"
  //                                   0     1         2        3        4
*/
// ELRS 2.0:
//  1 : Set Lua [Packet Rate]= 0 - 50Hz / 1 - 150Hz / 3 - 250Hz
//  2 : Set Lua [Telem Ratio]= 0 - off / 1 - 1:128 / 2 - 1:64 / 3 - 1:32 / 4 - 1:16 / 5 - 1:8 / 6 - 1:4 / 7 - 1:2
//  3 : Set Lua [Switch Mode]=0 -> Hybrid;Wide
//  4 : Set Lua [Model Match]=0 -> Off;On
//  5 : Set Lua [TX Power]=0 - 10mW / 1 - 25mW / 2 - 50mW /3 - 100mW/4 - 250mW
// 3 Default Settings
#define SETTING_1_PktRate 2 // 250Hz
#define SETTING_1_Power 1   // 25mW

#define SETTING_2_PktRate 1 // 150Hz
#define SETTING_2_Power 3   // 100mW

#define SETTING_3_PktRate 3 // 500Hz
#define SETTING_3_Power 1   // 25mW

enum chan_order
{
    AILERON,
    ELEVATOR,
    THROTTLE,
    RUDDER,
    AUX1, // (CH5)  ARM switch for Expresslrs
    AUX2, // (CH6)  angel / airmode change
    AUX3, // (CH7)  flip after crash
    AUX4, // (CH8)
    AUX5, // (CH9)
    AUX6, // (CH10)
    AUX7, // (CH11)
    AUX8, // (CH12)
};

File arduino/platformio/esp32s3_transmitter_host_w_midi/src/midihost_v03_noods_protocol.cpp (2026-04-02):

#include <Arduino.h>
#include <Adafruit_TinyUSB.h>
#include <MIDI.h>

/*

FYI: Serial Monitor commands:
1 -> outputting only nood1a
2 -> outputting only nood1b
3 -> outputting only nood2a
4 -> outputting only nood2b
a -> outputting all noods (DEFAULT)
q -> outputting noodOutVal1
s -> toggle serial print values

*/

/*

WHAT RC VALUES DID I USE HERE????

*/

// create an instance of the Adafruit_USBD_MIDI class
Adafruit_USBD_MIDI usb_midi;
MIDI_CREATE_INSTANCE(Adafruit_USBD_MIDI, usb_midi, MIDI);

// define the MIDI callbacks
void handleNoteOn(byte channel, byte pitch, byte velocity);
void handleNoteOff(byte channel, byte pitch, byte velocity);
void handleControlChange(byte channel, byte data1, byte data2);

// methods
void writeValuesToOutputs();
void overrideNoodOutputValues();
void updateSelectedNoodSendIndex();
void calcNoodOutputValues();
void checkIncomingSerial();
void updateSerialPrintValues();
void serialPrintDebugValues();
void processMIDI(void);
uint8_t mapToActualMinMax_256(uint8_t val, uint8_t range);
uint16_t mapToActualMinMax_1024(uint16_t val, uint16_t range);

// define init functions
void initializeMidi();
void initializeNoodOutputs();

// which (GPIO) pins are connected to the noods?
#define noodOutPin1 5
#define noodOutPin2 4

// will contain the pwm values for the noods
uint16_t noodOutVal1 = 0;
uint16_t noodOutVal2 = 0;

// these variables are involved with the timing of the nood updates
long prevNoodWriteTime = 0;
uint16_t noodWriteInterval = 1000 / 60;

enum DEADBAND_INPUT_RANGE
{
  _256 = 127,
  _1024 = 1023
};

struct DeadbandMinMax
{
  uint16_t min;
  uint16_t max;
};

// I manually explored when the values at the receiver start moving. The values are capped off at the lower and upper end of the range.
// So, for both a 256 and 1024 range, I found the values where the receiver starts to move and where it stops moving.
DeadbandMinMax deadbandMinMax256 = {10, 117};
DeadbandMinMax deadbandMinMax1024 = {0, 1024}; // {130, 936}

byte channelToPrint = 255;

unsigned long prevSerialPrintMills;
unsigned long serialPrintInterval = 200;

unsigned long prevBitmashChangeChannelMills;
unsigned long bitmashChangeChannelInterval = 1000 / 5;
byte bitmashSendChannel = 0;

uint16_t bitmashed_out = 0;
uint16_t bitmashed_outs[] = {0, 0, 0, 0};

// this is the value amount that we subtract from 127, to allow some deadband between the nood values.
// Effectively, determines the resolution of the noods. 0 is no deadband, 127 is max deadband.
#define NOOD_VALUES_TRANSMISSION_BANDWIDTH 16

uint16_t n00dSegmentIdentifiers[] = {512, 640, 768, 896}; // corresponds to upper bits 100, 101, 110, 111 (based on a 10-bits range)
byte n00dSegmentMaxValue = (127 - NOOD_VALUES_TRANSMISSION_BANDWIDTH); // was 55 (== 63 - 8) -> maybe try 127 - 16? -> update: yes, this works fine!

byte bitmash_nood1a = 0;
byte bitmash_nood1b = 0;
byte bitmash_nood2a = 0;
byte bitmash_nood2b = 0;

bool bSerialPrintValues = false;

void setup()
{
  Serial.begin(115200);

  pinMode(LED_BUILTIN, OUTPUT);
  digitalWrite(LED_BUILTIN, LOW);

  initializeMidi();

  initializeNoodOutputs();

  Serial.println("ready for action");
  digitalWrite(LED_BUILTIN, HIGH);
}

void loop()
{
  checkIncomingSerial();

  // handles cycling through the n00d channels at fixed intervals
  updateSelectedNoodSendIndex();

  calcNoodOutputValues();

  // DEBUG -> hard overwrite -> use to test the reliability of the approach
  if (channelToPrint != 255)
  {
    overrideNoodOutputValues();
  }

  if (bSerialPrintValues)
  {
    updateSerialPrintValues();
  }

  // set the value of the noods every so often (ie: not EVERY loop - not necessary)
  if (millis() - prevNoodWriteTime > noodWriteInterval)
  {

    ledcWrite(0, bitmashed_out); // bitmashed_out
    ledcWrite(1, noodOutVal2);

    prevNoodWriteTime = millis();
  }

  // read any new MIDI messages
  // DO NOT INTRODUCE A DELAY -> the usbMIDI.read() needs to be called rapidly from loop()
  MIDI.read();
}

void initializeMidi()
{
  usb_midi.setStringDescriptor("TinyUSB MIDI");

  // Initialize MIDI, and listen to all MIDI channels
  // This will also call usb_midi's begin()
  MIDI.begin(MIDI_CHANNEL_OMNI);

  MIDI.setHandleNoteOn(handleNoteOn);
  MIDI.setHandleNoteOff(handleNoteOff);
  MIDI.setHandleControlChange(handleControlChange);

  // wait until device mounted
  while (!TinyUSBDevice.mounted())
    delay(1);
}

void initializeNoodOutputs()
{
  // define pwm out pins
  ledcSetup(0, 10000, 10); // Setup channel at specified Hz with 8 (0-255), 12 (0-4095), or 16 (0-65535) bit resolution
  ledcSetup(1, 10000, 10); // Setup channel at specified Hz with 8 (0-255), 12 (0-4095), or 16 (0-65535) bit resolution

  ledcAttachPin(noodOutPin1, 0);
  ledcAttachPin(noodOutPin2, 1);
}

void updateSelectedNoodSendIndex()
{
  if (millis() - prevBitmashChangeChannelMills > bitmashChangeChannelInterval)
  {
    bitmashSendChannel++;
    if (bitmashSendChannel > 3)
    {
      bitmashSendChannel = 0;
    }

    prevBitmashChangeChannelMills = millis();
  }
}

void calcNoodOutputValues()
{
  switch (bitmashSendChannel)
  {
  case 0:
    bitmashed_out = n00dSegmentIdentifiers[0];
    bitmashed_out += map(bitmash_nood1a, 0, 127, 0, n00dSegmentMaxValue);
    break;
  case 1:
    bitmashed_out = n00dSegmentIdentifiers[1];
    bitmashed_out += map(bitmash_nood1b, 0, 127, 0, n00dSegmentMaxValue);
    break;
  case 2:
    bitmashed_out = n00dSegmentIdentifiers[2];
    bitmashed_out += map(bitmash_nood2a, 0, 127, 0, n00dSegmentMaxValue);
    break;
  case 3:
    bitmashed_out = n00dSegmentIdentifiers[3];
    bitmashed_out += map(bitmash_nood2b, 0, 127, 0, n00dSegmentMaxValue);
    break;
  }

  bitmashed_out = mapToActualMinMax_1024(bitmashed_out, DEADBAND_INPUT_RANGE::_1024);
  bitmashed_outs[bitmashSendChannel] = bitmashed_out;
}
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

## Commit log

2026-04-02 add xiao esp32c3 code
2026-04-02 add xiao esp32s3 code
2026-04-02 add wemos esp32s2 code
2026-04-02 Create xiao esp32s3 2nd transmitter drive v01.noisette
2026-04-23 add CRSF lib to esp32c3 project
2026-04-23 add CRSF lib to esp32s2 project
2026-04-23 add CRSF lib to esp32s3 project
2026-04-23 create esp32s3 project (copy from esp32s2 project)
2026-04-23 set esp32s3 project config
2026-04-23 esp32c3 - add scripts and update project config
2026-04-23 add cad files
    [Jaha Koo - Toad - pcb housing v1 - bottom.3mf, Jaha Koo - Toad - pcb housing v1 - top.3mf, Jaha Koo - Toad - servo motor mount.3mf]
2026-04-23 add Dynamixel driver board project
    [Dynamixel Interface Pro v2.kicad_pcb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]
2026-04-23 add interactive bom
2026-04-23 add toad host pcb project
    [toad_mainboard_v03.kicad_pcb, toad_mainboard_v03.kicad_sch]
2026-04-23 add custom Kicad footprints and symbols

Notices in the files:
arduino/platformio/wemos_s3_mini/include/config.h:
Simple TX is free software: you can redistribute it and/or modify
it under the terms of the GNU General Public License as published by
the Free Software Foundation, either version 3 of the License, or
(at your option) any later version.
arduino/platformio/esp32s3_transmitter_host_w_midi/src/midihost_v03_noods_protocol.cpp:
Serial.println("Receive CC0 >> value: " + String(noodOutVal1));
